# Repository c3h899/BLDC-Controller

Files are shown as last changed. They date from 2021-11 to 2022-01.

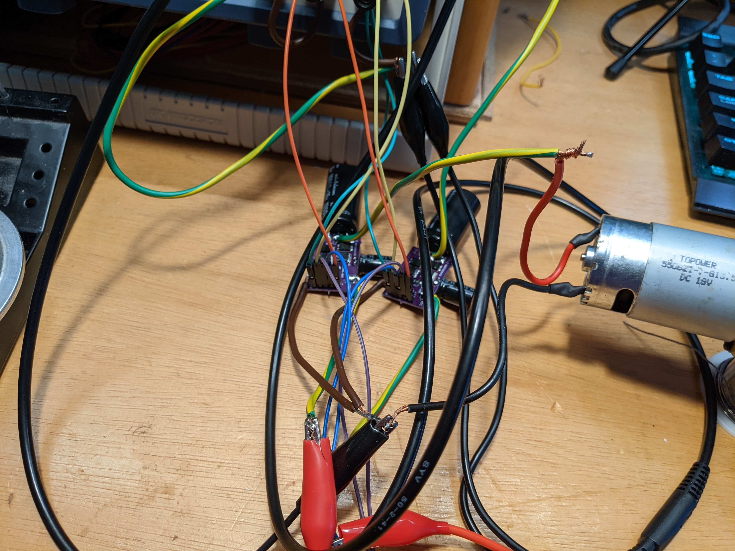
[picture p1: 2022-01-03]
Working Proto [Images]/PXL_20211218_214720438.jpg

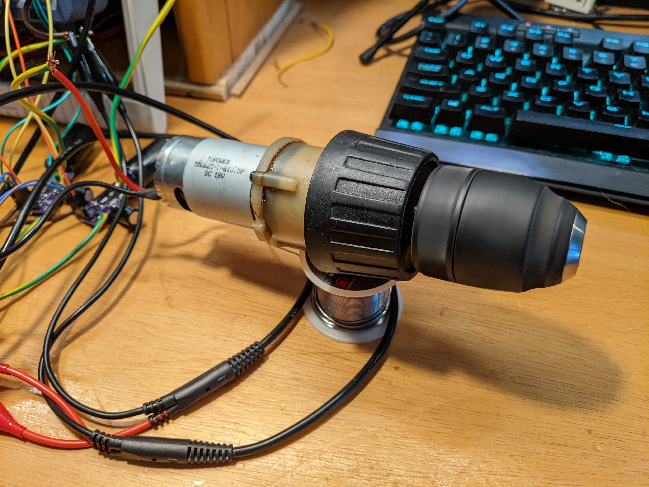
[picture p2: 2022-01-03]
Working Proto [Images]/PXL_20211218_214731544.jpg

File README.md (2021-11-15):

# Introduction
A basic implementation of a half-bridge driver for hobbyest DC motors.

## Features of Interest
* Isolated, Schmitt Trigger, Digital Input
* Designed for 3-phase operation of upto 2 HP
* Nominally, functional upto a few 100 kHz* 
* Mild protection from cross-conduction

## Summary of Critical Parts
* Isolated ADUM7234 Gate Driver
* 74HC7002 Schmitt-Trigger Input Stage
* BUK9T14-80E N-Channel MOSFET(s)
* NO Back-EMF Sensing

## Nominal Operation
* (12 to 30) V Drive input
* Several Amps (Heatsinking Required)
* **Expectes** Proper cross-conduction prevention measures in software

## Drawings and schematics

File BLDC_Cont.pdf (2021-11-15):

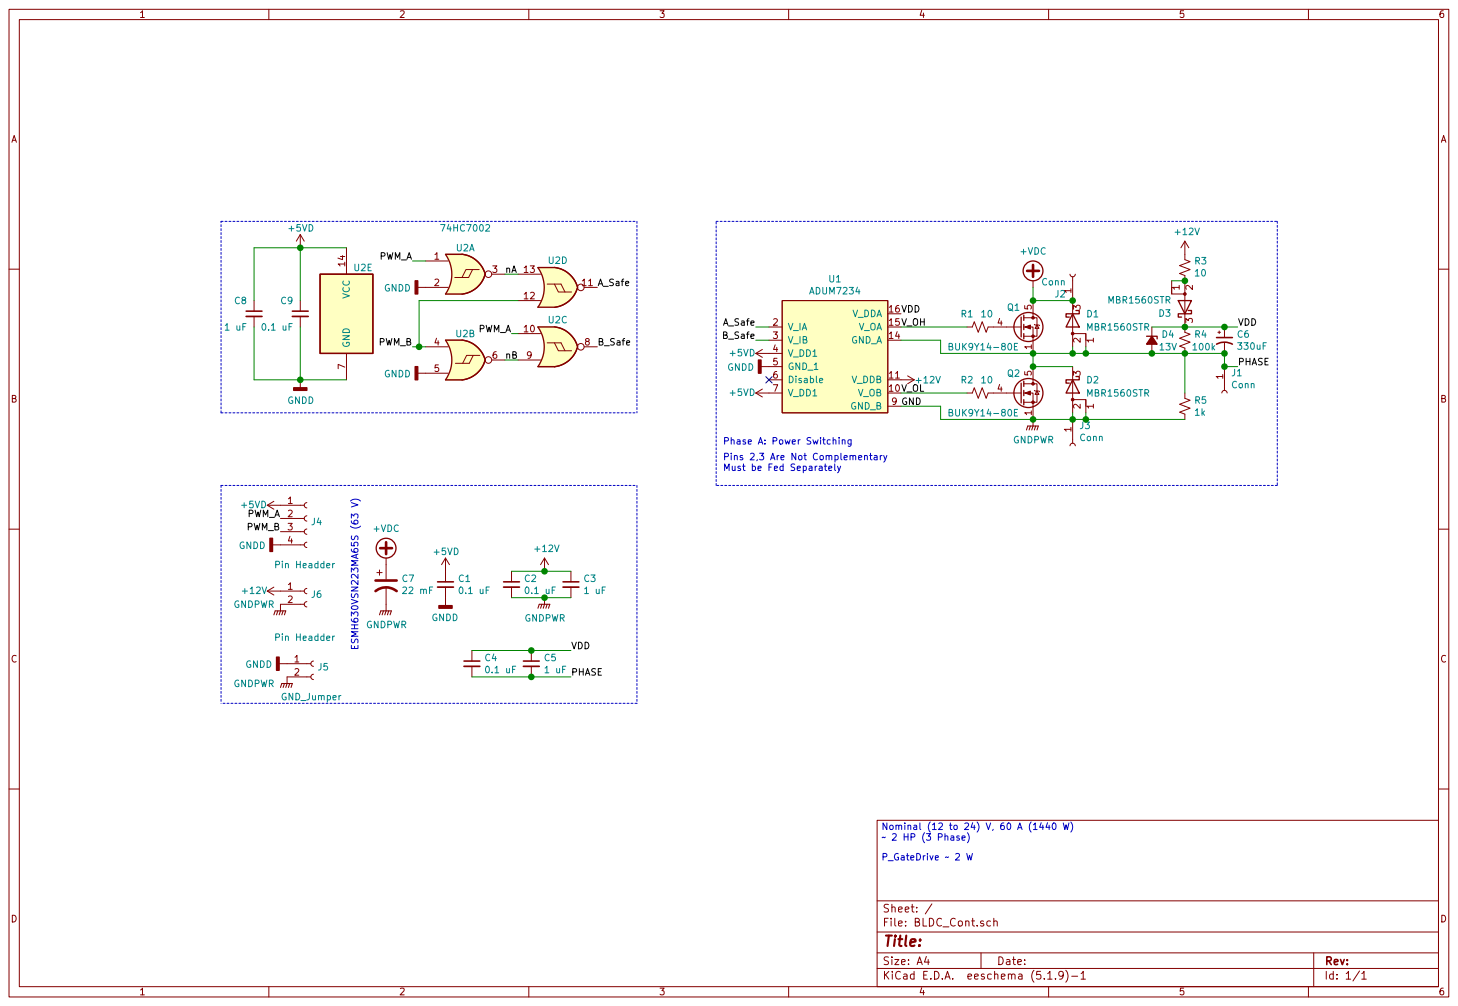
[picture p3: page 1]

Phase A: Power Switching
Pins 2,3 Are Not Complementary

Must be Fed Separately ESMH630VSN223MA65S (63 V)

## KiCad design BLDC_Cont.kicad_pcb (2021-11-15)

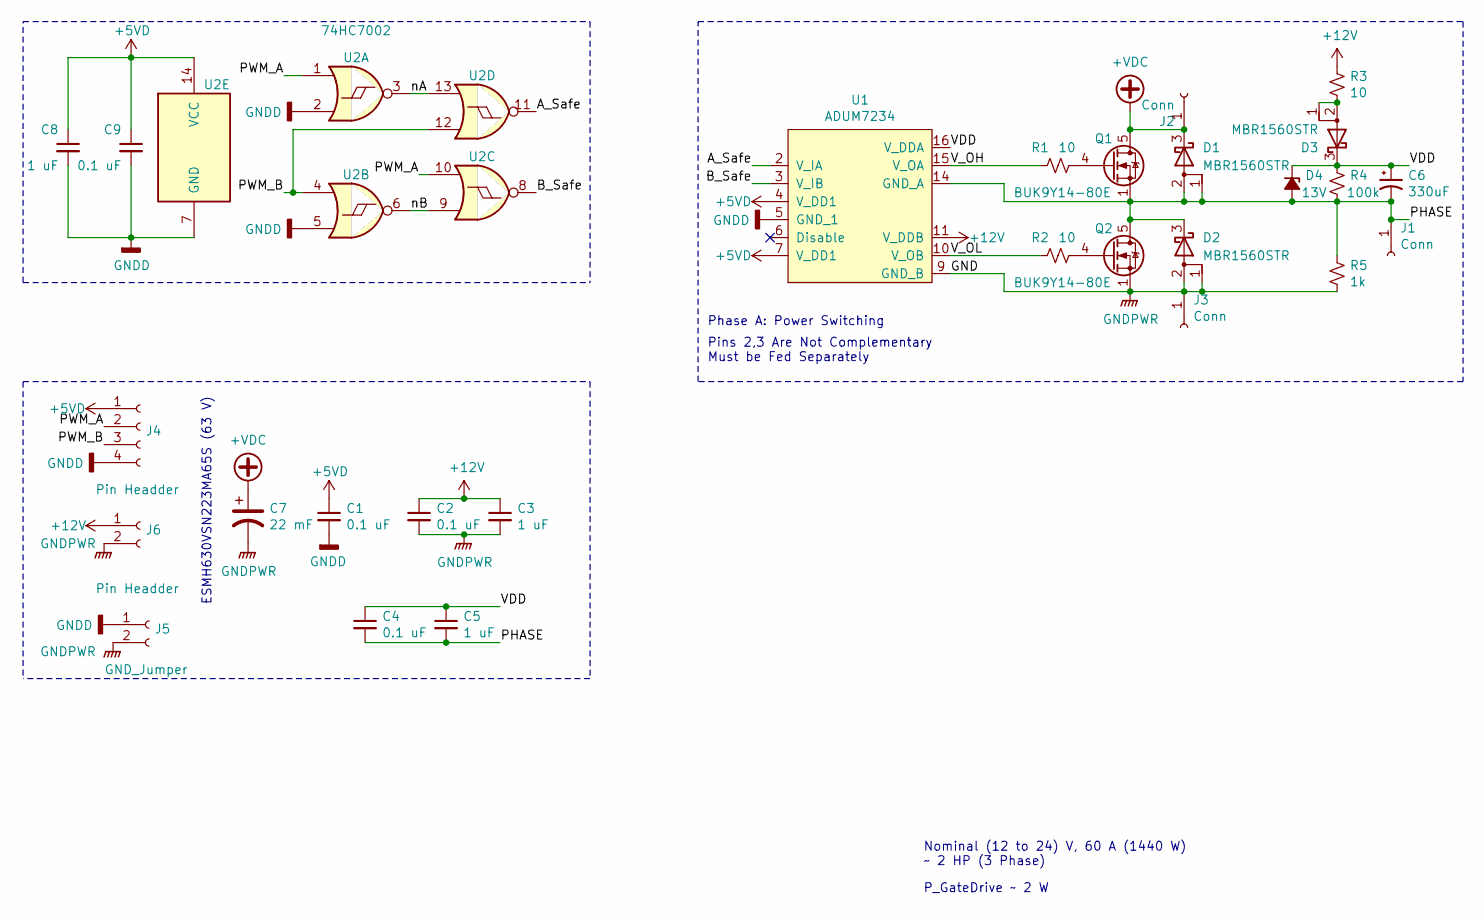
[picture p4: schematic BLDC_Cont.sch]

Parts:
C1, C2, C4, C9: 0.1 uF; C_1206_3216Metric_Pad1.33x1.80mm_HandSolder
C3, C5, C8: 1 uF; C_1206_3216Metric_Pad1.33x1.80mm_HandSolder
C6: 330uF; CP_Radial_D6.3mm_P2.50mm
C7: 22 mF; CP_Radial_D35.0mm_P10.00mm_SnapIn
D1, D2, D3: MBR1560STR; TO-277B
D4: 13V; D_SOD-123
J1, J2, J3: Conn; TestPoint_Pad_4.0x4.0mm
J4: Pin Headder; PinHeader_1x04_P2.54mm_Vertical
J5: GND_Jumper; SolderJumper-2_P1.3mm_Open_Pad1.0x1.5mm
J6: Pin Headder; PinHeader_1x02_P2.54mm_Vertical
Q1, Q2: BUK9Y14-80E; LFPAK56
R1, R2, R3: 10; R_1206_3216Metric_Pad1.30x1.75mm_HandSolder
R4: 100k; R_1206_3216Metric_Pad1.30x1.75mm_HandSolder
R5: 1k; R_1206_3216Metric_Pad1.30x1.75mm_HandSolder
U1: ADUM7234; SOIC-16_3.9x9.9mm_P1.27mm
U2: 74HC7002; SOIC-14_3.9x8.7mm_P1.27mm

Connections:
+5VD: C1.1, C8.1, C9.1, J4.1, U1.4 (V_DD1), U1.7 (V_DD1), U2.14 (VCC)
+12V: C2.1, C3.1, J6.1, R3.2, U1.11 (V_DDB)
+VDC: C7.1, D1.3 (K), J2.1, Q1.5 (D)
/A_Safe: U1.2 (V_IA), U2.11
/B_Safe: U1.3 (V_IB), U2.8
/PHASE: C4.2, C5.2, C6.2, D1.1 (A), D1.2 (A), D2.3 (K), D4.2 (A), J1.1, Q1.1 (S), Q1.2 (S), Q1.3 (S), Q2.5 (D), R4.2, R5.1, U1.14 (GND_A)
/PWM_A: J4.2, U2.1, U2.10
/PWM_B: J4.3, U2.4, U2.12
/VDD: C4.1, C5.1, C6.1, D3.3 (K), D4.1 (K), R4.1, U1.16 (V_DDA)
/V_OH: R1.2, U1.15 (V_OA)
/V_OL: R2.2, U1.10 (V_OB)
/nA: U2.3, U2.13
/nB: U2.6, U2.9
GNDD: C1.2, C8.2, C9.2, J4.4, J5.1, U1.5 (GND_1), U2.2, U2.5, U2.7 (GND)
GNDPWR: C2.2, C3.2, C7.2, D2.1 (A), D2.2 (A), J3.1, J5.2, J6.2, Q2.1 (S), Q2.2 (S), Q2.3 (S), R5.2, U1.9 (GND_B)
unnamed: D3.1 (A), D3.2 (A), R3.1
unnamed: Q1.4 (G), R1.1
unnamed: Q2.4 (G), R2.1

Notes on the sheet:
Nominal (12 to 24) V, 60 A (1440 W) ~~ 2 HP (3 Phase)
P_GateDrive ~~ 2 W
Phase A: Power Switching
ESMH630VSN223MA65S (63 V)
Pins 2,3 Are Not Complementary Must be Fed Separately

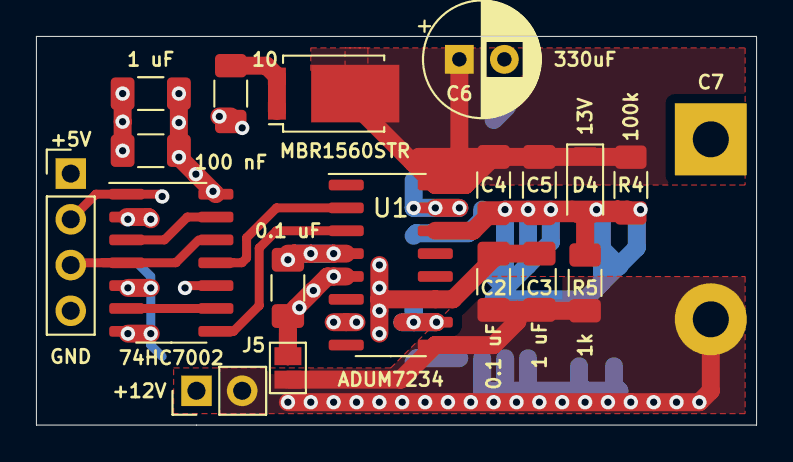
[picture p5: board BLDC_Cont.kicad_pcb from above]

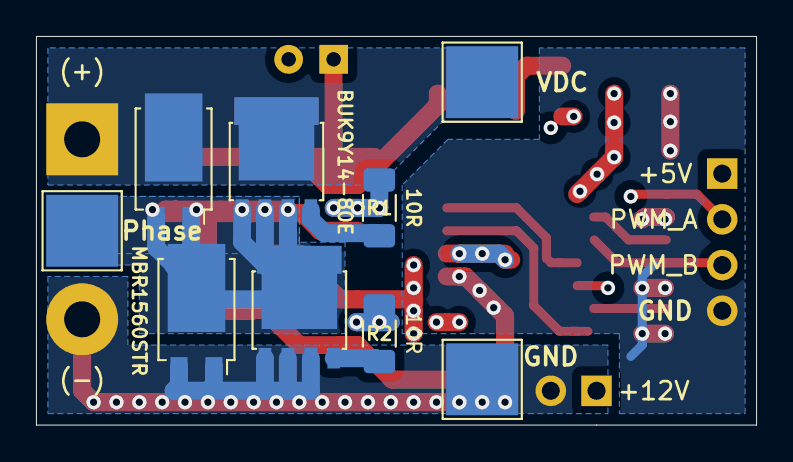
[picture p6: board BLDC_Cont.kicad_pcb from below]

Board: 4 copper layers, 40.0 x 21.6 mm, 28 parts (9 on the bottom side), 18 nets.

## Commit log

2021-11-07 Initial Upload
    Initial Upload of Project Initially Investigated in October
    Still in prototype construction & verification phase.
    [BLDC_Cont-B_Cu.gbr, BLDC_Cont-B_Fab.gbr, BLDC_Cont-B_Mask.gbr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]
2021-11-15 Rev. 3
    Updated Revision (3)
    -Organized files
    -Removed legacy documentation
    -Found cross-conduction protection of ADuM7234 was **NOT** satisfactory.
    +Added NOR gate based mutual exclusion circuit.
    [BLDC_Cont-B_Cu.gbr, BLDC_Cont-B_Fab.gbr, BLDC_Cont-B_Mask.gbr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]
